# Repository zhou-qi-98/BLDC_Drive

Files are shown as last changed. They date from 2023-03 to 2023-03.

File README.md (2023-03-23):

# 三相无刷直流电机驱动设计

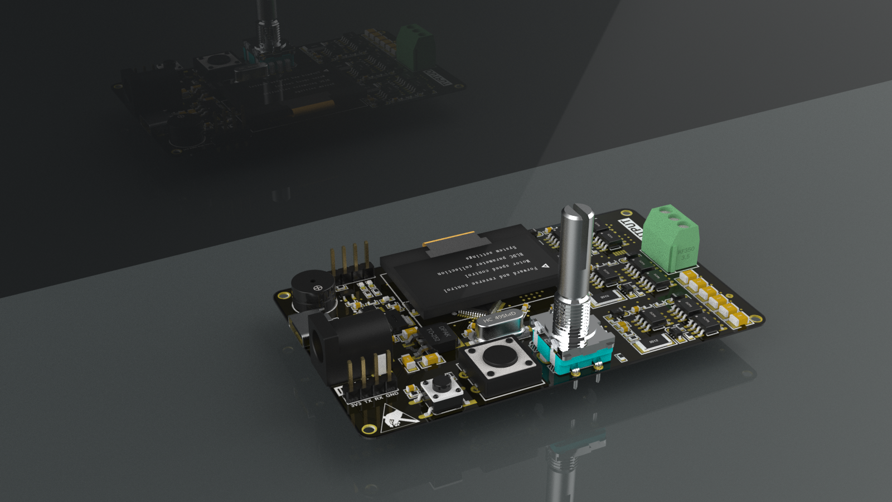
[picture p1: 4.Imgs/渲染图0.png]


#### 介绍
**stm32直流电机控制**
* 采用STM32F103C6T6A作为主控
* 主控与驱动分离
* 采用三相逆变桥电路
* 采集三相电流
* 前级采用栅极驱动MOS，自带闭锁
* 采集电机驱动电压，与MOS电流

无刷直流电机取消了电刷和换向器，从而失去了机械的磁场换向机构，磁场换向通过传感器检测转子位置，利用转子的位置信息来控制由开关电子器件构成的换向电路来达到磁场换向的目的。在无刷直流电机发展伊始，工程师们使用模拟电路来检测转子位置和控制开关器件。随着数字信号处理器、永磁材料和电力电子器件技术的飞速发展，无刷直流电机技术向数字化，智能化迈进。

在现阶段的无刷直流电机的设计中，一款优秀的驱动器设计是十分重要的。驱动器需要正确检测到转子位置信息，而且需要可靠的控制算法来控制功率器件的开通和关断，从而实现精度高、稳定性强的控制效果。

目前，无刷直流电机的主要控制方法有：PID控制、模糊控制、滑模变结构控制、基于神经网络的控制、基于锁相环的控制等。PID控制中P是指比例，I是指积分，D是指微分。通过调整这三个参数，来实现在不同运动状态下生成不同的控制量，来控制对象来达到理想的运动状态。但是由于只有三个可调参数使得控制精度不够，所以导致其在一些需要精密控制的领域不能发挥作用。模糊控制和滑模变结构控制都是非线性的控制方式，模糊控制是运用模糊数学的理论来对一些变量比较多的复杂系统来进行控制，滑模变结构控制是让控制对象在不同的控制逻辑下来回切换，由于此时处于滑动运动状态，对未知干扰的敏感降低，使系统有比较好鲁棒性。其余的控制方式各有特点，在特定领域能对无刷直流电机有良好的控制。

在位置检测领域，一般就有位置传感器检测法和无位置传感器检测法。位置传感器有电磁式的，可以安装在定子组件上，来检测转子永磁体转动，通过磁场的变化记录转子位置信息，也有光电式的，将光源和接收器安装在定子组件上，转子上安装遮光板，当转子转动时，接收器产生的脉冲信号则是转子位置信息。无位置传感器检测法有一种H. Lehuy等人提出的反电动势检测法，这种方法不需要在电机内安装位置传感器，简化了系统的结构。还有一些学者提出过续流二极管法和基于定子磁链估计法等无位置传感器检测法。

#### 六步法
六步法中的三相电机每次只有两组绕组有电流通过，产生磁场。为了让电机旋转，一般按照Q1Q2—Q2Q3—Q3Q4—Q4Q5—Q5Q6—Q6Q1的顺序依次导通功率开关管
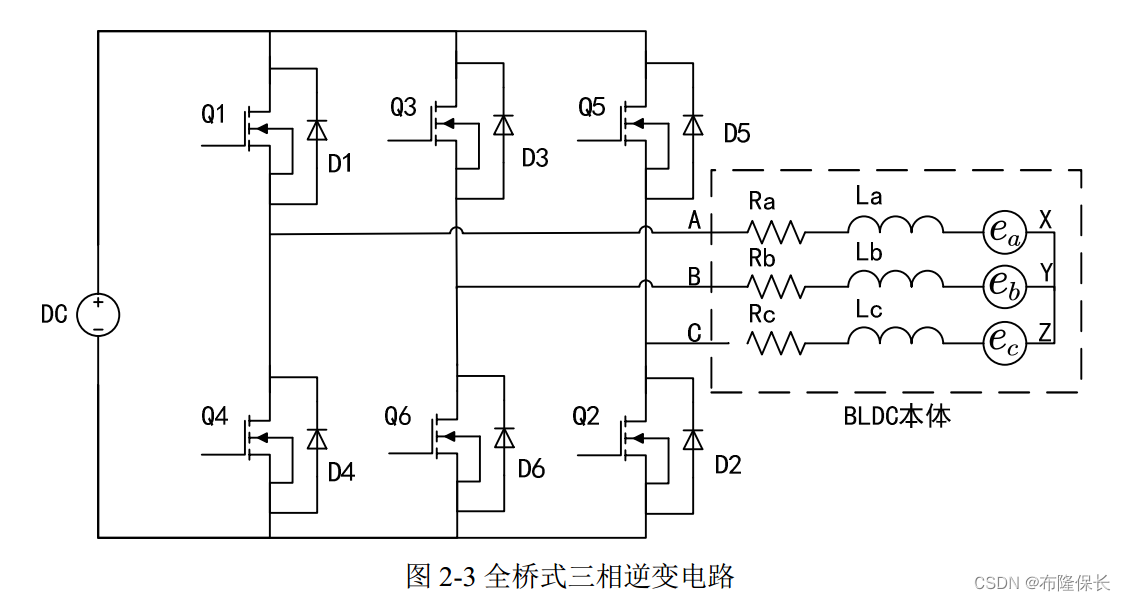
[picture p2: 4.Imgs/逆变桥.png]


#### 反电动势检测法
当转子上的永磁体旋转时，会切割绕组产生反电动势，而且转速越大，其产生的反电动势也越大，这个反电动势是可以使用检测电路检测的。检测三相绕组中反电动势，根据其变化，就可以得知转子是否到达六个关键换向节点，并决定是否进行换相操作。

无刷直流电机产生的反电动势是呈梯形波形状的，而其定子电流是断续的方波形状。因为在电机转动过程中，定子中总有两相绕组会通过电流，使那两相绕组中也会生成大小相等、方向相反的反电动势。等其中一相绕组断开时，其电流立即降为零，但是反电动势会通过开关管和二极管进行续流，会由正变负或者由负变正，与下一段电流反向时的反电动势接续。在一个周期中，每相的反电动势有两次过零点，三相则可以接收到6次过零点信号，滞后30°+60°k（k=0，1，2…）后即为开关管换相的信号。
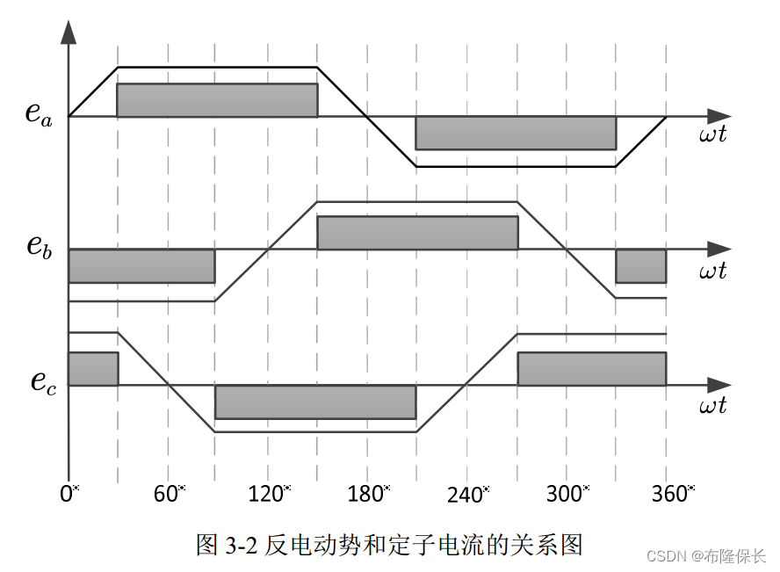
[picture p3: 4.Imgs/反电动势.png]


#### 原理图
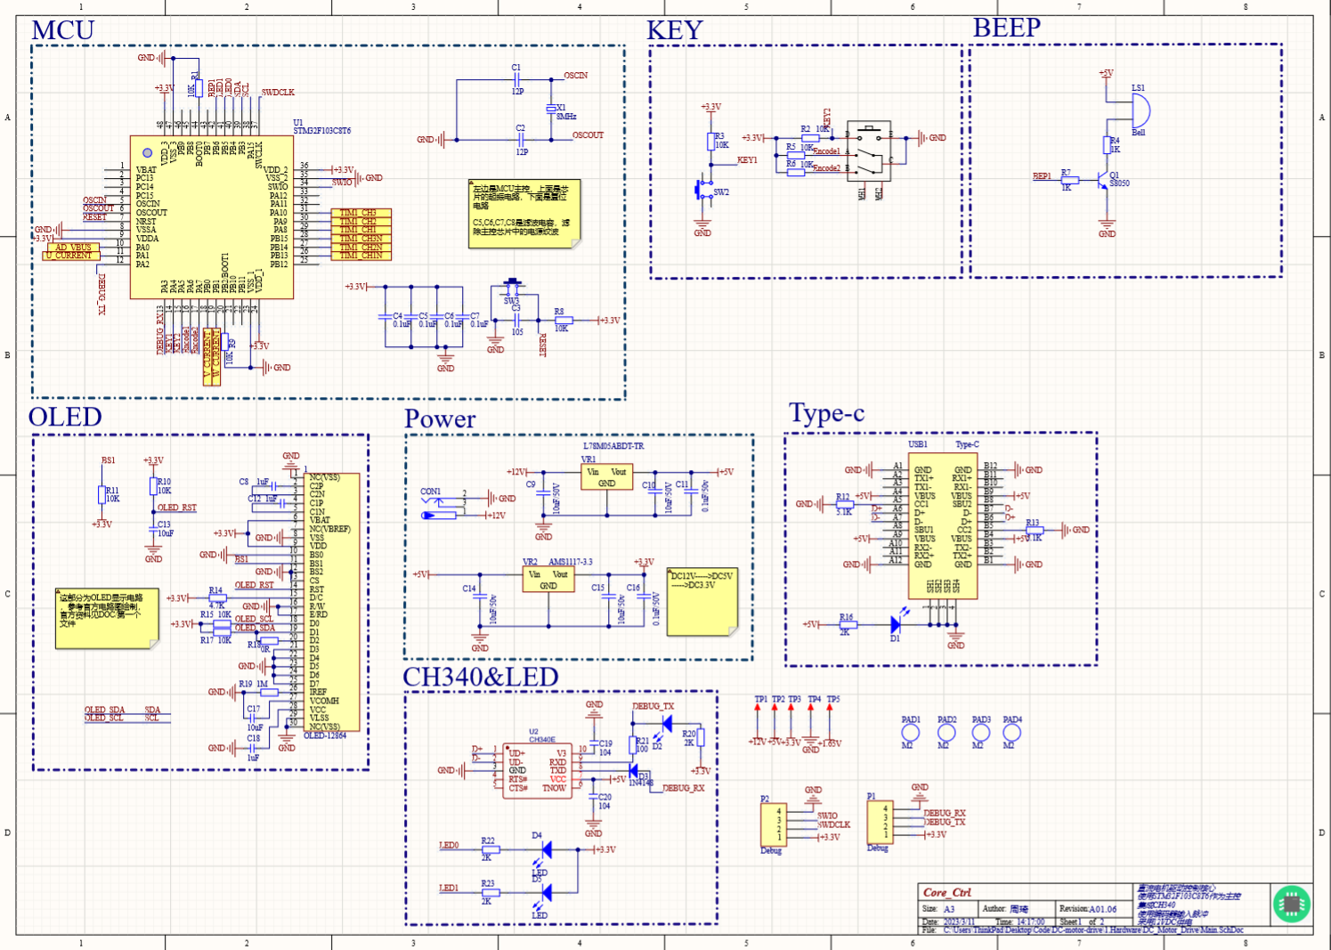
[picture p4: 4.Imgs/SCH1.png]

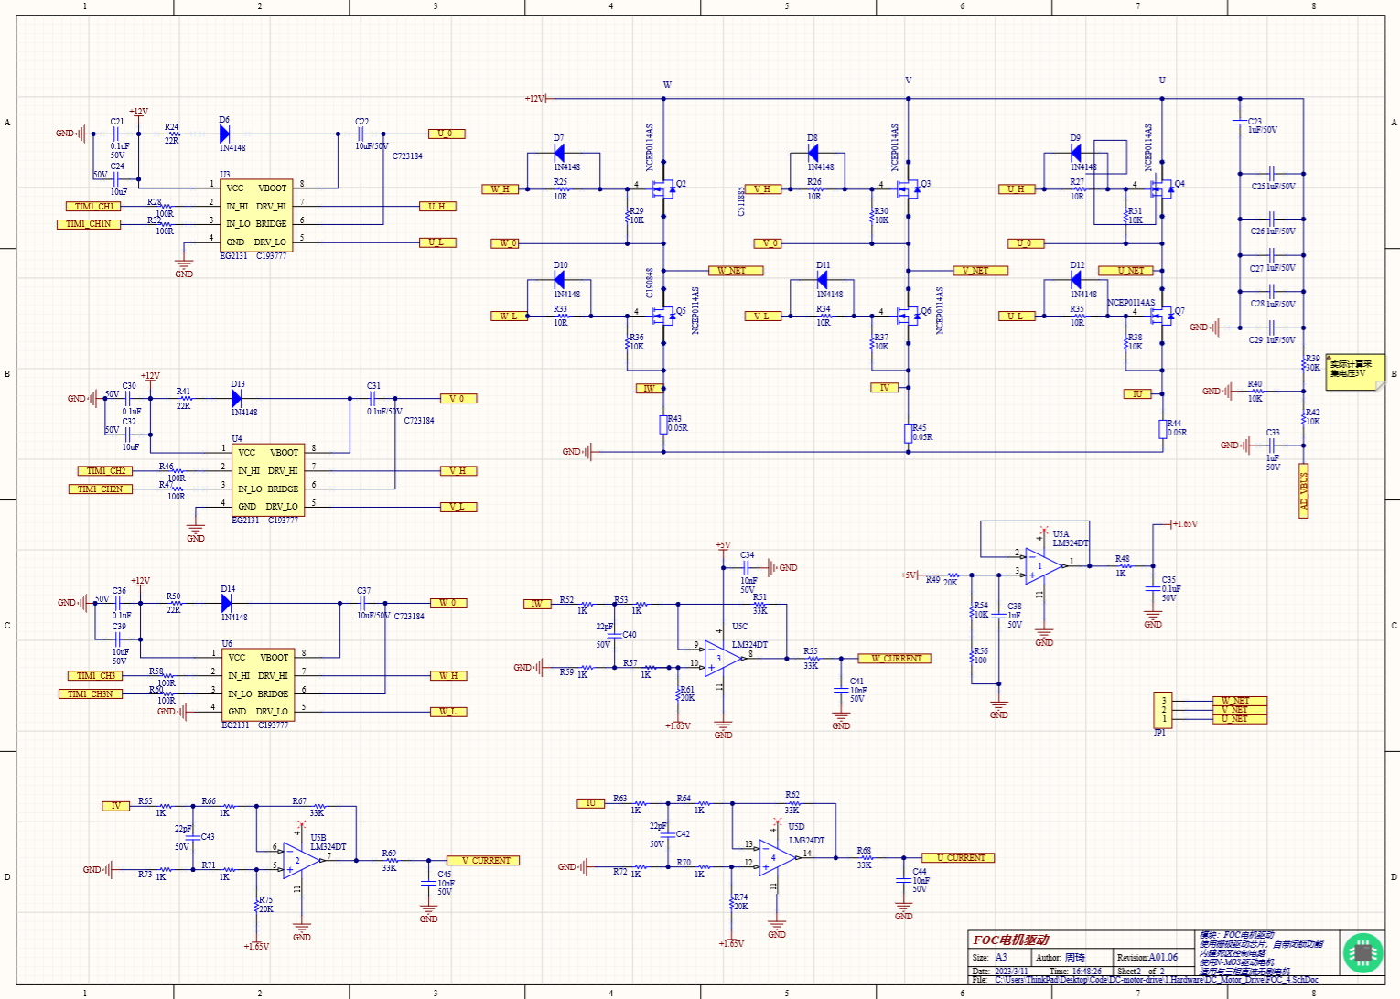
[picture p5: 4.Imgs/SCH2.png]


#### PCB
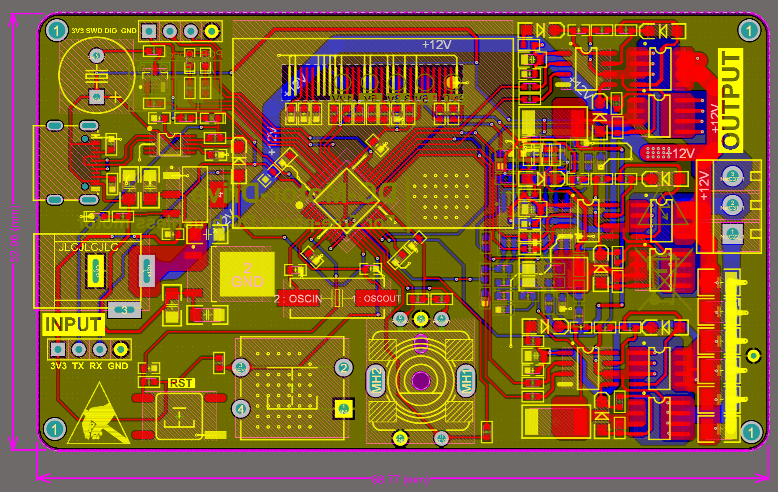
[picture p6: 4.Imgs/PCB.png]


#### 软件架构
* 分时调度

#### 参与贡献
* [爱学习的王大可](https://gitee.com/zhouqi98)
* [幺幺零1223](https://gitee.com/one-zero-1223)

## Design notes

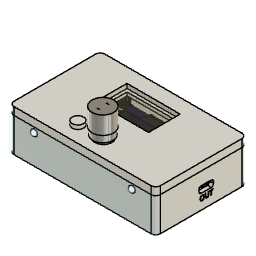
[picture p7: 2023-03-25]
1.Hardware/DC_Motor1 v24.png

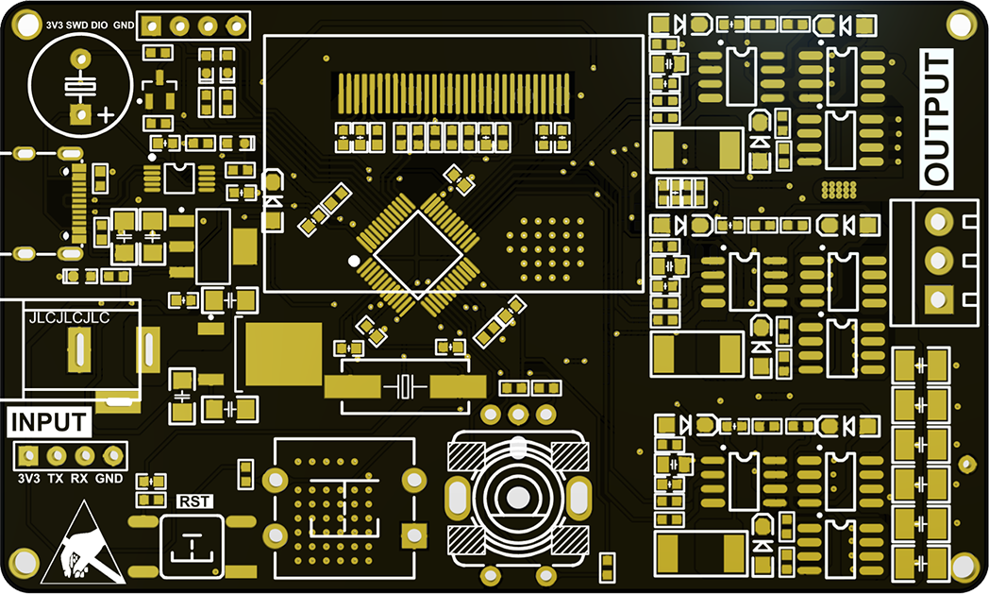
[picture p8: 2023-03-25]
4.Imgs/贴图3.png

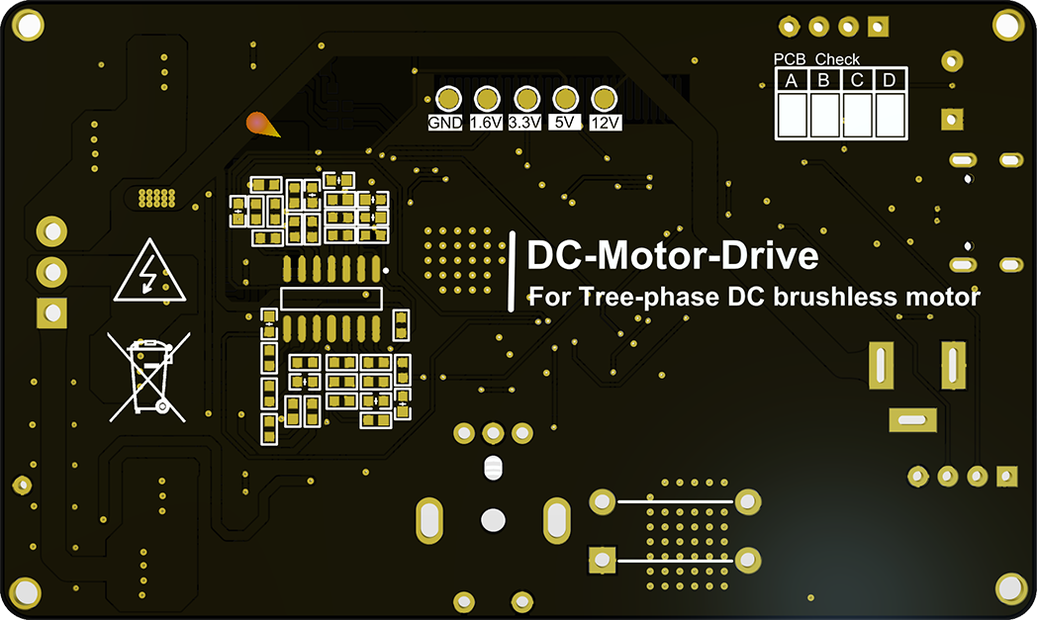
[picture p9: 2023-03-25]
4.Imgs/贴图4.png

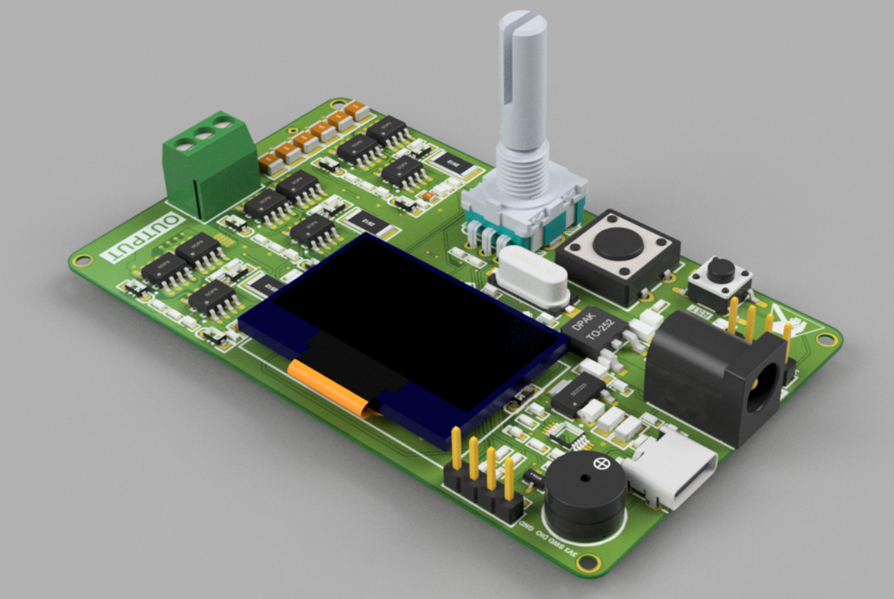
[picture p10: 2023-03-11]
4.Imgs/渲染图1.png

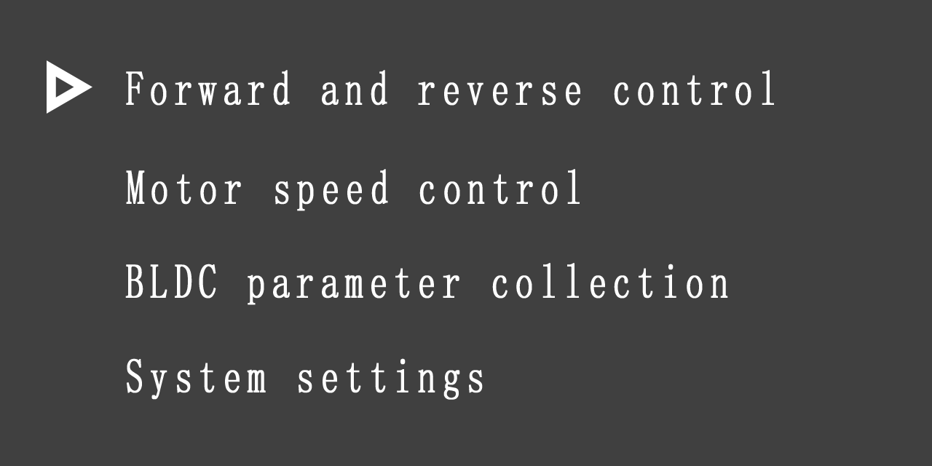
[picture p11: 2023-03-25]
4.Imgs/oled.png

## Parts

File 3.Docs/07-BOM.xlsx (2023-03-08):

Comment | Description | Designator | Footprint | LibRef | Quantity
OLED-12864 | 显示屏 | 1 | OLED-12864-1.3-TOP | OLED-12864 | 1
12P | 贴片电容 | C1, C2 | C0603_L | C | 2
105 | 贴片电容 | C3 | C0603_L | C | 1
0.1uF | 贴片电容, [NoValue] | C4, C5, C6, C7, C21, C30, C35, C36 | C0603_L | C, Cap | 8
1uF | Capacitor, [NoValue] | C8, C12, C18, C33, C38 | C0603_L | 电容-0402, Cap | 5
10uF/50V | C89632, [NoValue] | C9, C10, C14, C15 | C1206_L | Cap | 4
0.1uF/50v |  | C11 | C1206_L | Cap | 1
10uF | Capacitor | C13, C17 | C0603_L | 电容-0402 | 2
0.1uF/50V | C89632 | C16, C31 | C0603_L | Cap | 2
104 | 无极性贴片电容 | C19, C20 | C0603_L | C | 2
10uF/50V | C89632 | C22, C37 | C0603_L | Cap | 2
1uF/50V |  | C23, C25, C26, C27, C28, C29 | C1210_L | Cap | 6
10uF |  | C24, C32, C39 | C0805_L | Cap | 3
10nF |  | C34, C41, C44, C45 | C0603_L | Cap | 4
22pF |  | C40, C42, C43 | C0603_L | Cap | 3
3.5*1.3 | 低压电源接口 | CON1 | DC-005 | P-DC | 1
LED0 | 发光二极管 | D1 | LED0603_R | LED0 | 1
LED0 | 发光二极管 | D2 | LED0603_G | LED0 | 1
1N4148 | 整流二极管, 二极管 | D3, D6, D7, D8, D9, D10, D11, D12, D13, D14 | SOD-123 | M7, SOD-323 1N4148WS T4 | 10
LED | 发光二极管 | D4, D5 | LED0603_B | LED | 2
HDR-1X3 | 3P接插件 | JP1 | KF350-3P | Header 3 | 1
Bell | Electrical Bell | LS1 | BEEP 5x9x5.5 | Bell | 1
Debug | Header, 4-Pin | P1, P2 | HDR2.54-LI-4P | Header 4 | 2
M2 | 铜柱孔 | PAD1, PAD2, PAD3, PAD4 | M2 | M3 | 4
S8050 | 高频放大-NPN型 | Q1 | SOT23-3N | 8050-SMD | 1
NCEP0114AS | C190848 | Q2, Q3, Q4, Q5, Q6, Q7 | SOP8 | NMOS-2 | 6
10K | 贴片电阻, Resistor | R1, R2, R3, R5, R6, R8, R9, R10, R11, R15, R17, R29, R30, R31, R36, R37, R38, R40, R42, R54 | R0603_L | R, 电阻-0402, Res1 | 20
1K | Resistor | R4, R7, R48, R52, R53, R57, R59, R63, R64, R65, R66, R70, R71, R72, R73 | R0603_L | 电阻-0402, Res1 | 15
5.1K | Resistor | R12, R13 | R0603_L | 电阻-0402 | 2
4.7K | Resistor | R14 | R0603_L | 电阻-0402 | 1
2K | Resistor, 贴片电阻 | R16, R20, R22, R23 | R0603_L | 电阻-0402, R | 4
0R | Resistor | R18 | R0603_L | 电阻-0402 | 1
1M | Resistor | R19 | R0603_L | 电阻-0402 | 1
100 | Resistor | R21, R56 | R0603_L | 电阻-0402, Res1 | 2
22R | Resistor | R24, R41, R50 | R0603_L | Res1 | 3
10R | Resistor | R25, R26, R27, R33, R34, R35 | R0603_L | Res1 | 6
100R | Resistor | R28, R32, R46, R47, R58, R60 | R0603_L | Res1 | 6
30K | Resistor | R39 | R0603_L | Res1 | 1
0.05R | 电流检测电阻 | R43, R44, R45 | R2512_L | R-I | 3
20K | Resistor | R49, R61, R74, R75 | R0603_L | Res1 | 4
33K | Resistor | R51, R55, R62, R67, R68, R69 | R0603_L | Res1 | 6
EC11K1524406 |  | SW1 | SW-TH_EC11K1524406 | EC11K1524406 | 1
12x12x5 | 直插12x12轻触开关 | SW2 | SW DIP-12*12*4.3 | TSW DIP-12x12 | 1
6x6x5 | 贴片6x6轻触开关 | SW3 | SW SMD-6*6*5 | TSW SMD-6x6 | 1
TEST | 测试点 | TP1, TP2, TP3, TP4, TP5 | TEST 1.6 | TEST | 5
STM32F103C8T6 |  | U1 | LQFP48-7*7 | STM32F103C8T6 | 1
CH340E |  | U2 | MSOP10_M | CH340E | 1
EG2131 | C193777 | U3, U4, U6 | SOP8 | NCP5106BDR2G | 3
LM324DT | 运放 | U5 | SOIC-14 | LM324DT_[C71035] | 1
Type-C |  | USB1 | USB-C-SMD_16P | USB-Type-C-TOP | 1
L78M05ABDT-TR | 低压差线性稳压(LDO) | VR1 | TO-252 | TO-252-2 L78M05ABDT-TR | 1
AMS1117-3.3 | 低压差线性稳压(LDO) | VR2 | SOT223_L | SOT-223 AMS1117-3.3 | 1
8MHz | 2脚无源脚晶振 | X1 | OSC HC-49SMD | XTAL-2P | 1

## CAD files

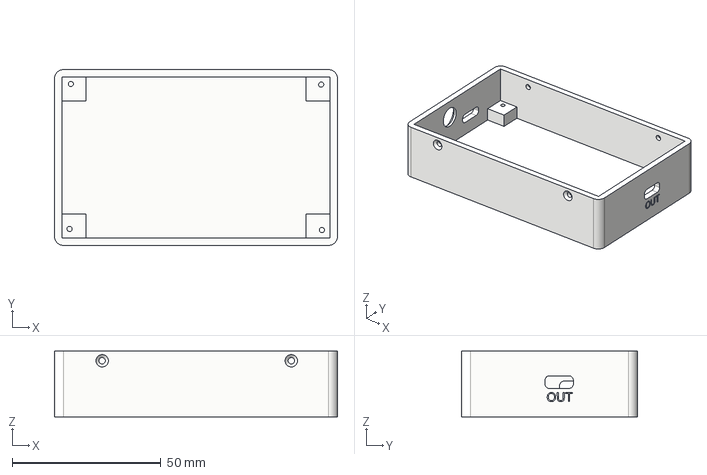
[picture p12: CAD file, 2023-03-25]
1.Hardware/底部.step
95.0 x 59.0 x 22.0 mm

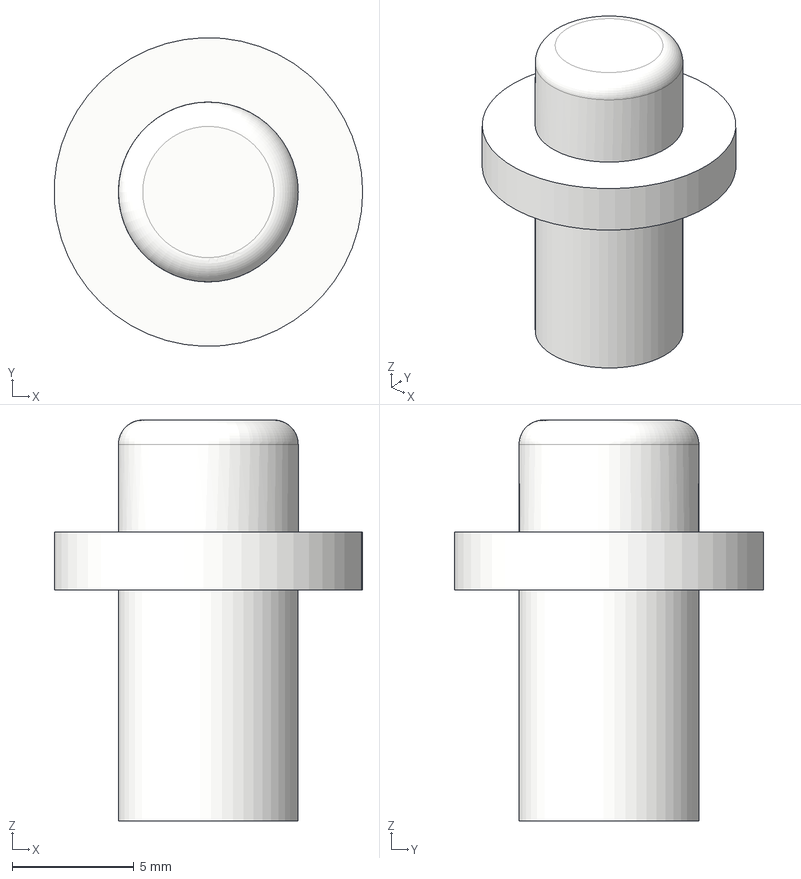
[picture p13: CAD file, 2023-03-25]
1.Hardware/按钮.step
12.7 x 12.7 x 16.5 mm

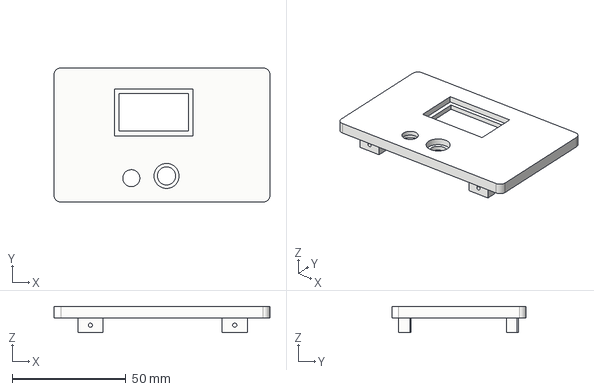
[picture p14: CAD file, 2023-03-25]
1.Hardware/盖子.step
95.0 x 59.0 x 11.5 mm

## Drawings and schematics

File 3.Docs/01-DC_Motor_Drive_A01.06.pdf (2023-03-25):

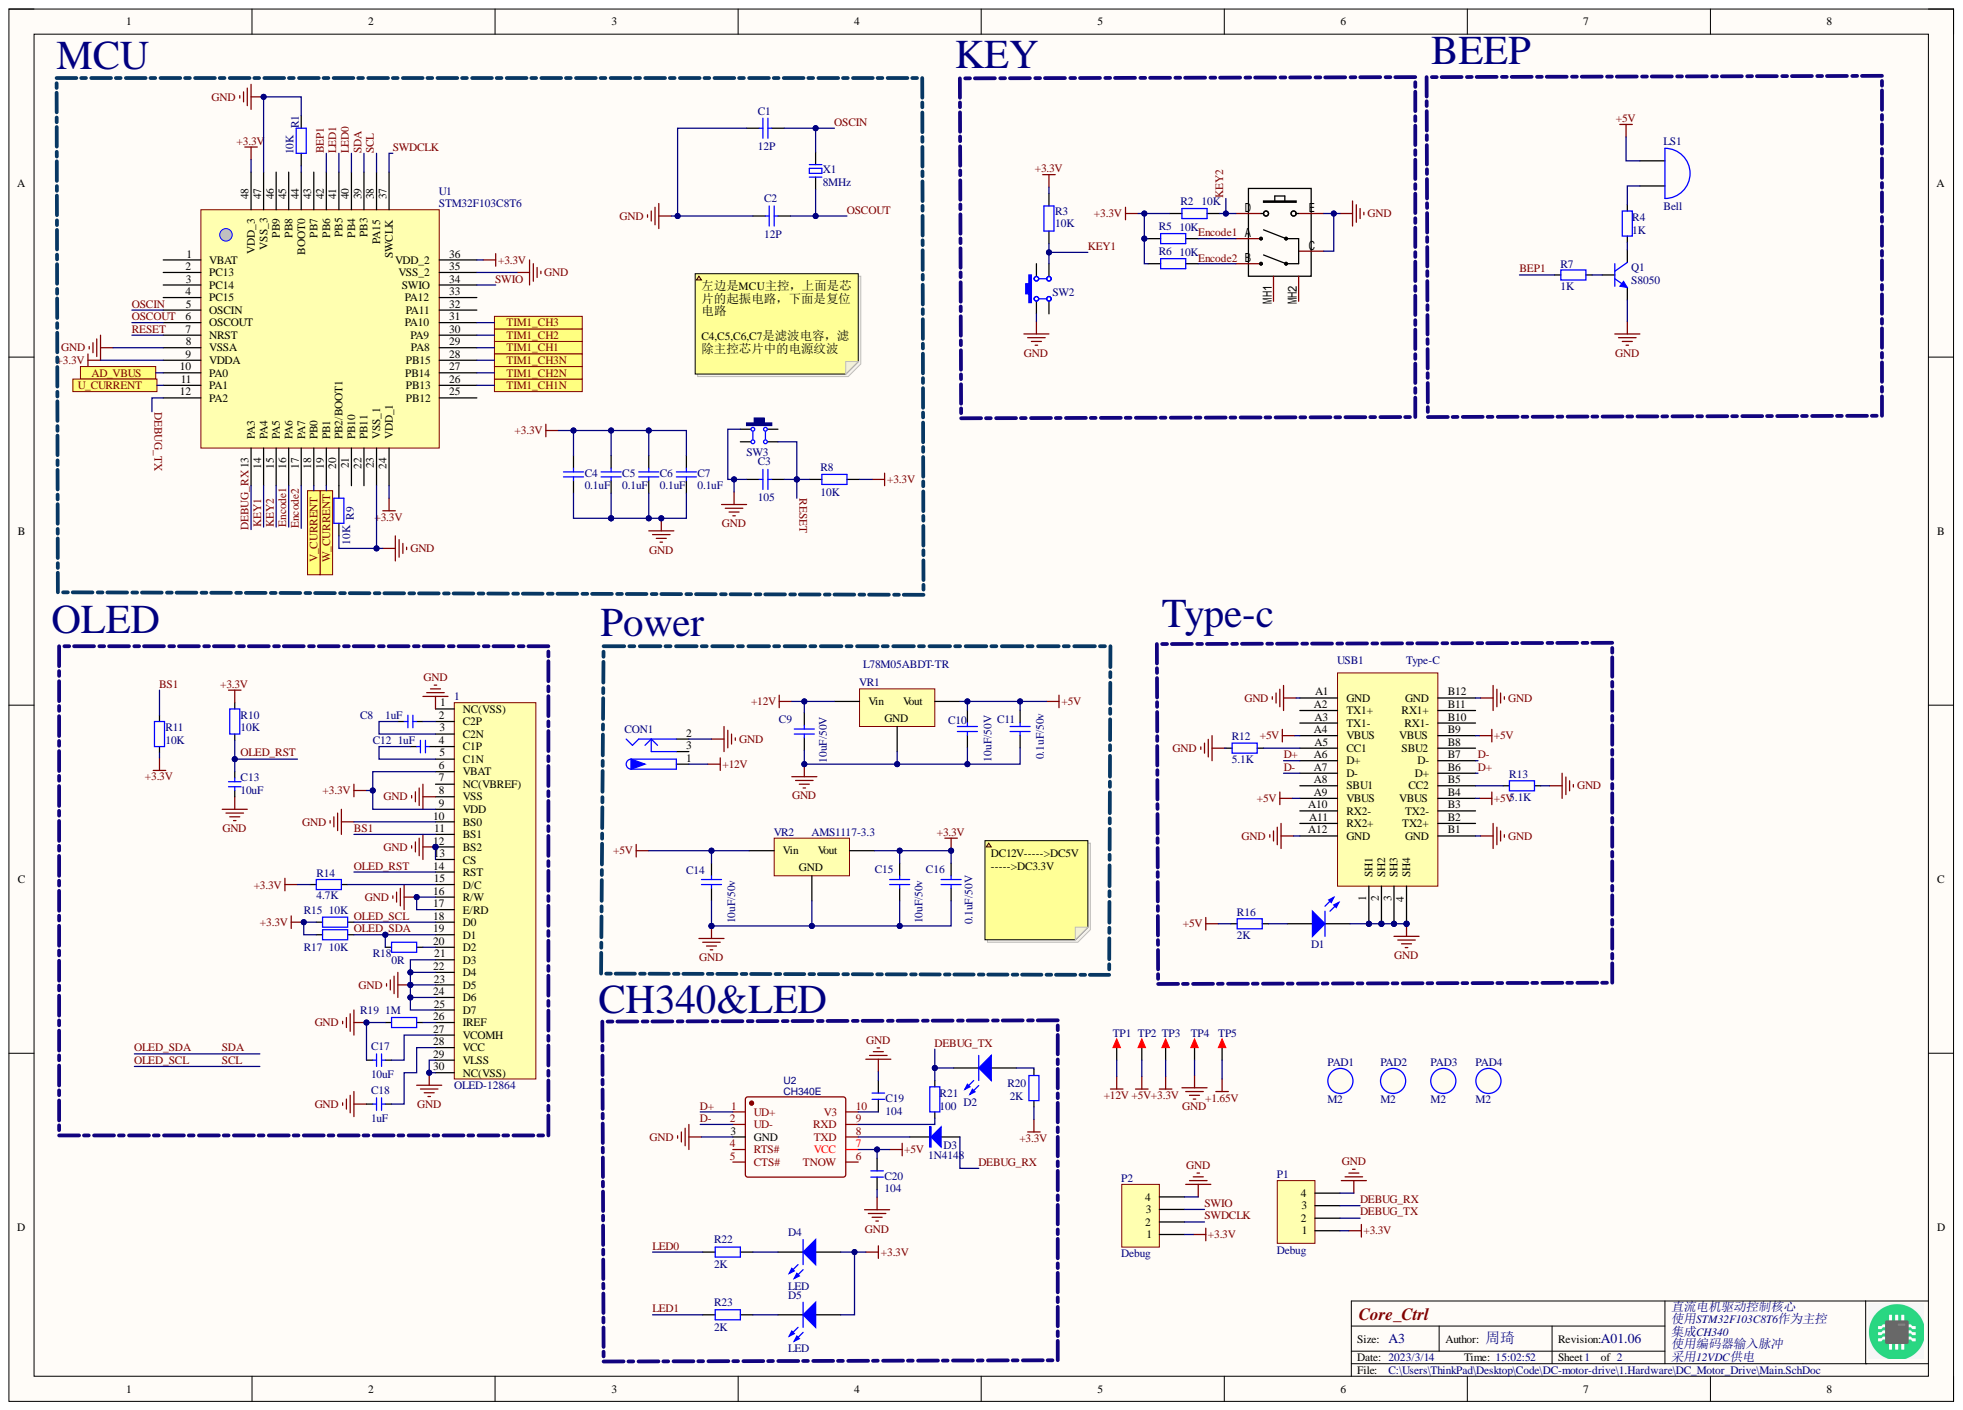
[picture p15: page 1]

左边是MCU主控，上面是芯 片的起振电路，下面是复位

VDDA 9 | | TIM1_CH3N

AD_VBUS | | PA1 11 | | TIM1_CH2N
U_CURRENT | | | | TIM1_CH1N

C17 | | VCOMH 27

VCC 28
VLSS 29
NC(VSS) 30

C:\Users\ThinkPad\Desktop\Code\DC-motor-drive\1.Hardware\DC_Motor_Drive\Main.SchDoc

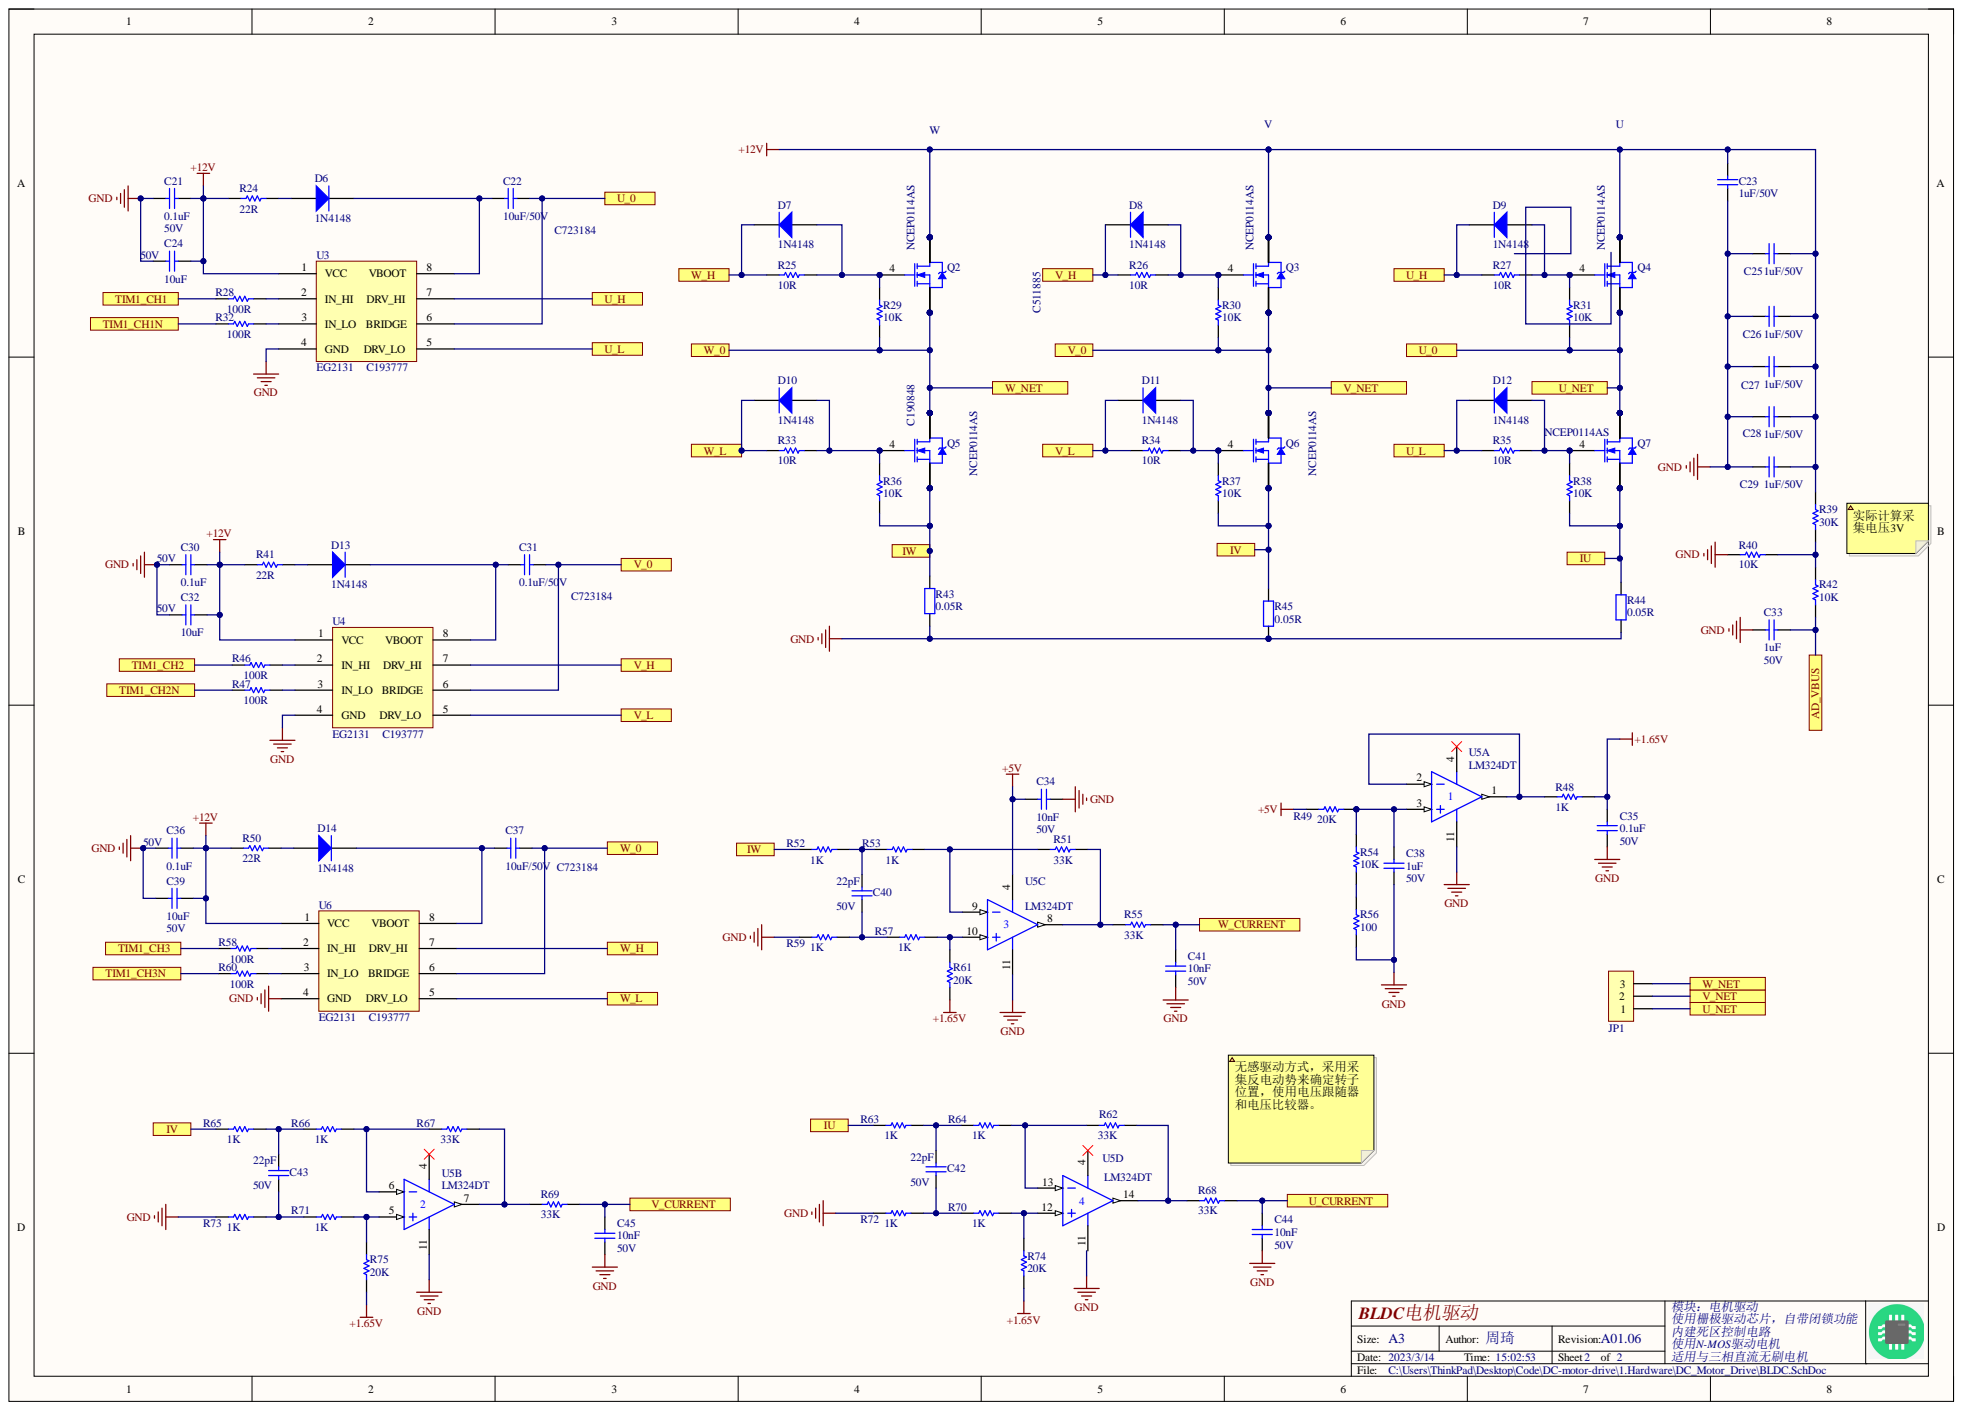
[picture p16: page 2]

C:\Users\ThinkPad\Desktop\Code\DC-motor-drive\1.Hardware\DC_Motor_Drive\BLDC.SchDoc

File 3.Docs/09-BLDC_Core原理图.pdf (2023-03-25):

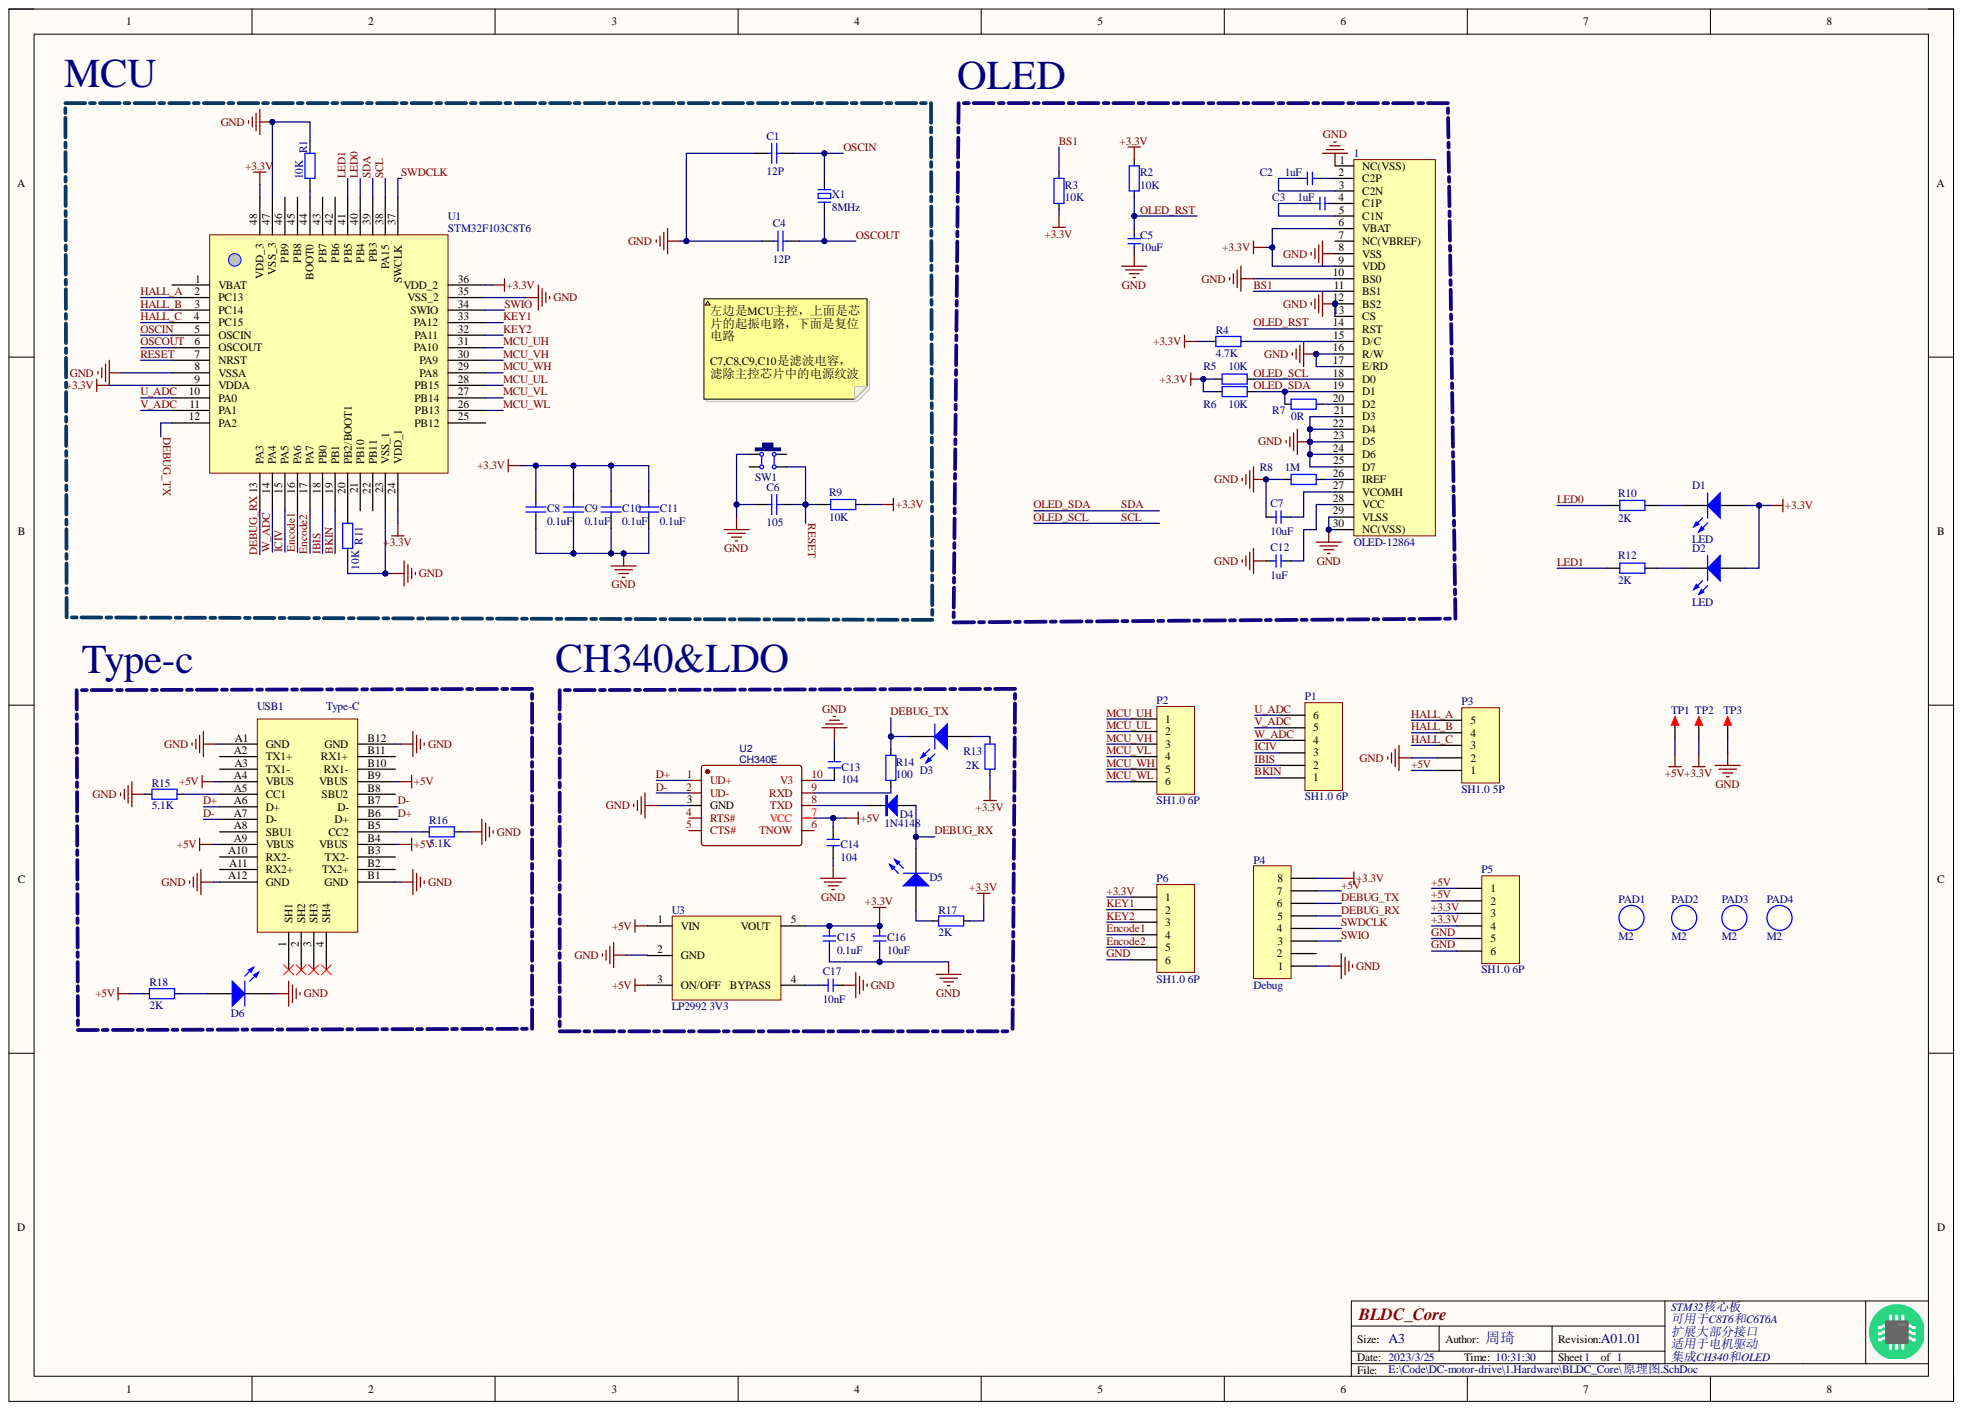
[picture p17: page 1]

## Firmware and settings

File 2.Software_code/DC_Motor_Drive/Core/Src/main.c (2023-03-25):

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
/* Includes ------------------------------------------------------------------*/
#include "main.h"
#include "adc.h"
#include "iwdg.h"
#include "tim.h"
#include "usart.h"
#include "gpio.h"

/* USER CODE BEGIN Includes */
//以下开始用户头文件，这里的头文件在MY文件夹内
#include "stdio.h"
#include "User_Scheduler.h"
#include "User_Function.h"
#include "IIC_OLED.h"
#include "key.h"
#include "bmp.h"
#include "Motor.h"
/* USER CODE END Includes */

/* USER CODE BEGIN PD */
#define VERSION      "A01.0D"//主版本号子版本号.修正版本号

/*---->
版本更新历史
A01.0D: 新增速度变量，实现编码器控制 2023/3/25 13:18
A01.0C: 多级菜单功能完成 2023/3/24 20:36
A01.0B: 编码器功能初步测试通过 2023/3/15 21:39
A01.0A: 调度器/OLED等外设测试通过 2023/3/15 20:49
A01.09: 新增按键扫描函数(待验证) 2023/3/14 14:08
A01.08: 新增ADC校准，规范代码(待验证) 2023/3/11 17:19
A01.07: 新增看门狗，溢出时间约6.5s(待验证) 2023/3/11 16:42
A01.06: 采集四个通道的ADC数据(待验证) 2023/3/11 16:30
A01.05: OLED移植成功(待验证) 2023/3/11 15:54
A01.04: 新增用户调度器(未验证) 2023/3/11 15:36
A01.03: 重写printf函数，修改至串口二 2023/3/11 15:19
A01.02: 宏定义管LED,BEEP外设管脚 2023/3/11 15:06
A01.01: 新建工程，初始化外设 2023/3/11 14:55
*/

/* USER CODE END PD */

/* USER CODE BEGIN PM */
volatile uint8_t SYS_TIME1S_FLAG = 0;//计数1s标志位
int8_t led_status;
/* USER CODE END PM */


void SystemClock_Config(void);
/* USER CODE BEGIN 0 */
/*-----------------------------------------*/
/*-----重定义printf函数--------------------*/
/*-----函数名：int fputc(int ch, FILE *f)--*/
/*-----------------------------------------*/
int fputc(int ch, FILE *f){
	uint8_t temp[1] = {ch};
	HAL_UART_Transmit(&huart2, temp, 1, 2);//huart2需要根据你的配置修改
	return ch;
}

/* USER CODE END 0 */

/**
  * @brief  The application entry point.
  * @retval int
  */
int main(void)
{
  /* MCU Configuration--------------------------------------------------------*/

  /* Reset of all peripherals, Initializes the Flash interface and the Systick. */
  HAL_Init();

  /* Configure the system clock */
  SystemClock_Config();

  /* Initialize all configured peripherals */
  MX_GPIO_Init();
  MX_TIM3_Init();
  MX_ADC1_Init();
  MX_TIM1_Init();
  MX_USART2_UART_Init();
  MX_IWDG_Init();
  MX_TIM2_Init();
  /* USER CODE BEGIN 2 */
	HAL_TIM_Base_Start_IT(&htim2);//开启定时器
  __HAL_TIM_CLEAR_IT(&htim3,TIM_IT_UPDATE);

	HAL_TIM_Encoder_Start(&htim3, TIM_CHANNEL_ALL);//启动计数
  __HAL_TIM_ENABLE_IT(&htim3,TIM_IT_UPDATE);

	HAL_ADCEx_Calibration_Start(&hadc1); //ADC校准

	BEEP_OFF;
	OLED_Init();			//OLED初始化
	OLED_CLS();				//OLED清屏
	//OLED_ShowStr(16,4,(unsigned char*)"SYS init succeeded      ",1);
	OLED_DrawBMP(0,0,128,8,BMP0);
	user_main_info("System initialization succeeded！");
	//MX_IWDG_Init();
	
	//HAL_TIM_PWM_Start(&htim1,TIM_CHANNEL_1);
  //HAL_TIMEx_PWMN_Start(&htim1,TIM_CHANNEL_1);
  //HAL_TIM_PWM_Start(&htim1,TIM_CHANNEL_2);
  //HAL_TIMEx_PWMN_Start(&htim1,TIM_CHANNEL_2);

	
	

	//TIM1->CCR1 = 50;//50%的占空比
	//HAL_TIM_PWM_Start(&htim1,TIM_CHANNEL_1);//V相正波
	/*
				HAL_TIM_PWM_Stop(&htim1,TIM_CHANNEL_1);//U相不发波
			HAL_TIMEx_PWMN_Stop(&htim1,TIM_CHANNEL_1);
			
			TIM1->CCR2 = 50;//50%的占空比
			HAL_TIM_PWM_Start(&htim1,TIM_CHANNEL_2);//V相正波
			
			TIM1->CCR3 = 50;//50%的占空比
			HAL_TIMEx_PWMN_Start(&htim1,TIM_CHANNEL_3);//V相正波
			*/
	
	//MX_IWDG_Init();
	//LED0_ON;
	
	
	/*开始控制电机*/
	//Motor_Stop();
	//ROTOR_Pre_positioning(1);
	//Motor_Start(1);
	
	
	
  /* USER CODE END 2 */

  /* Infinite loop */
  /* USER CODE BEGIN WHILE */
  while (1)
  {
    /* USER CODE END WHILE */

    /* USER CODE BEGIN 3 */
		Schedule();						/*调度器*/
		FuncRun(&tSysScanFlag);/*功能运行*/
		//Motor_Run(1);
		
  }
  /* USER CODE END 3 */
}

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
/* USER CODE BEGIN 4 */
/*下面开始子函数*/
/*中断服务函数*/
void HAL_TIM_PeriodElapsedCallback(TIM_HandleTypeDef *htim) 
	{
			if (htim->Instance == htim2.Instance) {//定时器2中断,这里1ms中断一次
					SYS_TIME1S_FLAG=1;
	    }
      if (htim->Instance == htim3.Instance)//外部中断3来源于编码器
      {
        
        if( ((int)(__HAL_TIM_IS_TIM_COUNTING_DOWN(&htim3)))== 0)//反向旋转
        {
          KEY_Value = 4;
        }else//正向旋转
        {
          KEY_Value = 3;
        }
        //user_main_info("编码器%d",KEY_Value);
      }

}
	



/* USER CODE END 4 */
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


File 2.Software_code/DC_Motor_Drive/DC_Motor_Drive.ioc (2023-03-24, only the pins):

Mcu.UserName=STM32F103C6Tx
PA0-WKUP.Signal=ADCx_IN0
PA1.Signal=ADCx_IN1
PA10.GPIO_Label=WH
PA10.Signal=GPIO_Output
PA13.Signal=SYS_JTMS-SWDIO
PA14.Signal=SYS_JTCK-SWCLK
PA15.GPIO_Label=IIC_SCL
PA15.Signal=GPIO_Output
PA2.Signal=USART2_TX
PA3.Signal=USART2_RX
PA4.GPIO_Label=KEY1
PA4.Signal=GPIO_Input
PA5.GPIO_Label=KEY2
PA5.Signal=GPIO_Input
PA6.Signal=S_TIM3_CH1
PA7.Signal=S_TIM3_CH2
PA8.GPIO_Label=UH
PA8.Signal=GPIO_Output
PA9.GPIO_Label=VH
PA9.Signal=GPIO_Output
PB0.Signal=ADCx_IN8
PB1.Signal=ADCx_IN9
PB13.GPIO_Label=UL
PB13.Signal=GPIO_Output
PB14.GPIO_Label=VL
PB14.Signal=GPIO_Output
PB15.GPIO_Label=WL
PB15.Signal=GPIO_Output
PB3.GPIO_Label=IIC_SDA
PB3.Signal=GPIO_Output
PB4.GPIO_Label=LED0
PB4.Signal=GPIO_Output
PB5.GPIO_Label=LED1
PB5.Signal=GPIO_Output
PB6.GPIO_Label=BEEP1
PB6.Signal=GPIO_Output
PD0-OSC_IN.Signal=RCC_OSC_IN
PD1-OSC_OUT.Signal=RCC_OSC_OUT

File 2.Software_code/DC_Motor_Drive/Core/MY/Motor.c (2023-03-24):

#include "Motor.h"

/*
//order 用于发波的标号
void Motor_run(uint8_t order,uint8_t Duty)
{
	switch(order)
	{
		//U0  V+ W-
		case 1:
		{
			HAL_TIM_PWM_Stop(&htim1,TIM_CHANNEL_1);//U相不发波
			HAL_TIMEx_PWMN_Stop(&htim1,TIM_CHANNEL_1);
			
			TIM1->CCR2 = ((float)Duty/(float)100)*70;//修改占空比
			HAL_TIM_PWM_Start(&htim1,TIM_CHANNEL_2);//V相正波
			
			TIM1->CCR3 = ((float)Duty/(float)100)*70;//50%的占空比
			HAL_TIMEx_PWMN_Start(&htim1,TIM_CHANNEL_3);//W相互补波
			break;	
		}
		
		case 3:
		{
			HAL_TIM_PWM_Stop(&htim1,TIM_CHANNEL_2);//v相不发波
			HAL_TIMEx_PWMN_Stop(&htim1,TIM_CHANNEL_2);
			
			TIM1->CCR1 = ((float)Duty/(float)100)*70;//修改占空比
			HAL_TIMEx_PWMN_Start(&htim1,TIM_CHANNEL_1);//V相互补波
			
			TIM1->CCR3 = ((float)Duty/(float)100)*70;//50%的占空比
			HAL_TIM_PWM_Start(&htim1,TIM_CHANNEL_3);//W相正波
			break;	
		}
		
		case 2:
		{
			HAL_TIM_PWM_Stop(&htim1,TIM_CHANNEL_3);//W相不发波
			HAL_TIMEx_PWMN_Stop(&htim1,TIM_CHANNEL_3);
			
			TIM1->CCR1 = ((float)Duty/(float)100)*70;//修改占空比
			HAL_TIMEx_PWMN_Start(&htim1,TIM_CHANNEL_1);//U相互补波
			
			TIM1->CCR2 = ((float)Duty/(float)100)*70;//50%的占空比
			HAL_TIM_PWM_Start(&htim1,TIM_CHANNEL_2);//V相正波
			break;	
		}
		case 6:
		{
			HAL_TIM_PWM_Stop(&htim1,TIM_CHANNEL_1);//U相不发波
			HAL_TIMEx_PWMN_Stop(&htim1,TIM_CHANNEL_1);
			
			TIM1->CCR3 = ((float)Duty/(float)100)*70;//修改占空比
			HAL_TIMEx_PWMN_Start(&htim1,TIM_CHANNEL_3);//U相互补波
			
			TIM1->CCR2 = ((float)Duty/(float)100)*70;//修改占空比
			HAL_TIM_PWM_Start(&htim1,TIM_CHANNEL_2);//V相正波
			break;	
		}
		case 4:
		{
			HAL_TIM_PWM_Stop(&htim1,TIM_CHANNEL_2);//V相不发波
			HAL_TIMEx_PWMN_Stop(&htim1,TIM_CHANNEL_2);
			
			TIM1->CCR3 = ((float)Duty/(float)100)*70;//修改占空比
			HAL_TIMEx_PWMN_Start(&htim1,TIM_CHANNEL_3);//W相互补波
			
			TIM1->CCR1 = ((float)Duty/(float)100)*70;//修改占空比
			HAL_TIM_PWM_Start(&htim1,TIM_CHANNEL_1);//U相正波
			break;	
		}
		case 5:
		{
			HAL_TIM_PWM_Stop(&htim1,TIM_CHANNEL_3);//W相不发波
			HAL_TIMEx_PWMN_Stop(&htim1,TIM_CHANNEL_3);
			
			TIM1->CCR2 = ((float)Duty/(float)100)*70;//修改占空比
			HAL_TIMEx_PWMN_Start(&htim1,TIM_CHANNEL_2);//V相互补波
			
			TIM1->CCR1 = ((float)Duty/(float)100)*70;//修改占空比
			HAL_TIM_PWM_Start(&htim1,TIM_CHANNEL_1);//V相正波
			break;	
		}
		default:break;
	}
}

*/
// 120 度HAL,如果你的电机直接用这个表驱动有问，那你可能需要根据
// 实际电机进行适当的调整对应关系，可在该表基础上进行适当修改即可
// 正 转
// 霍尔#1 霍尔#2 霍尔#3		A+ 		A- 		 B+ 		B- 		C+ 		C- 		方向
// 1 				0 		1 		关闭 		关闭 	关闭 	开通 	开通 		关闭 		↓   
// 0 				0 		1 		关闭 		开通 	关闭 	关闭 	开通 		关闭 		↓		
// 0 				1 		1 		关闭 		开通 	开通 	关闭 	关闭 		关闭 		↓			
// 0 				1 		0 		关闭 		关闭 	开通 	关闭 	关闭 		开通 		↓
// 1 				1 		0 		开通 		关闭 	关闭 	关闭 	关闭 		开通 		↓
// 1 				0 		0 		开通 		关闭 	关闭 	开通 	关闭 		关闭 		↓

// 反 转
// 霍尔#1 霍尔#2 霍尔#3 	A+ 		A- 			B+ 		B- 		C+ 		C- 		方向
// 1 				0 		1 		关闭 		关闭 	开通 	关闭 	关闭 		开通 		↑
// 0 				0 		1 		开通 		关闭 	关闭 	关闭 	关闭 		开通 		↑
// 0 				1 		1 		开通 		关闭 	关闭 	开通 	关闭 		关闭 		↑
// 0 				1 		0 		关闭 		关闭 	关闭 	开通 	开通 		关闭 		↑
// 1 				1 		0 		关闭 		开通 	关闭 	关闭 	开通 		关闭 		↑
// 1 				0 		0 		关闭 		开通 	开通 	关闭 	关闭 		关闭 		↑



/*
电机停机
*/
void Motor_Stop()
{
	//关三个上管，开三个下管，泄除反电动势
	
	//1.关上管
	UH_OFF;VH_OFF;WH_OFF;
	HAL_Delay(1);//延时下，防止上管未完全关闭 就导通下管，烧毁MOS
	//2.开下管
	UL_ON;VL_ON;WL_ON;	
}



/*
电机转子预定位
direction:转动方向，根据转动方向来进行调整
做三次预定位，确定转子定位到准确位置
*/
void ROTOR_Pre_positioning(uint8_t direction)
{
	if(direction)//正转
	{
			//1.开始做预定位
		for(uint8_t i = 0;i<3;i++)
		{
			UH_ON;VH_OFF;WH_OFF;//U+ W-
			UL_OFF;VL_OFF;WL_ON;
			HAL_Delay(10);
		}
			//此时转自应该在位置6	
	}
}


void Six_step(uint8_t step)
{
	switch(step)
	{
		case 1:
		{
			UH_ON;VH_OFF;WH_OFF;//U+ V-
			UL_OFF;VL_ON;WL_OFF;
			break;
		}
		case 2:
		{
			UH_OFF;VH_OFF;WH_ON;//V- W+
			UL_OFF;VL_ON;WL_OFF;
			break;
		}
		case 3:
		{
			UH_OFF;VH_ON;WH_OFF;//U- V+
			UL_ON;VL_OFF;WL_OFF;
			break;
		}
		case 4:
		{
			UH_OFF;VH_ON;WH_OFF;//U- V+
			UL_ON;VL_OFF;WL_OFF;
			break;
		}
		case 5:
		{
			UH_OFF;VH_ON;WH_OFF;//V+ W-
			UL_OFF;VL_OFF;WL_ON;
			break;
		}
		case 6:
		{
			UH_ON;VH_OFF;WH_OFF;//U+ W-
			UL_OFF;VL_OFF;WL_ON;
			break;
		}
		default:
		{
			//1.关上管
			UH_OFF;VH_OFF;WH_OFF;
			//2.开下管
			UL_ON;VL_ON;WL_ON;
			break;
		}
	
	}
}


/************* 启动加速 ******************/
void Motor_Start(uint8_t direction)
{
	if(direction)
	{
		for(uint8_t i=100; i>0; i-=2)
		{
			for(uint8_t j=1; j<7; j++)
			{
				Six_step(j);
			}
			HAL_Delay(i+1);//最低1MS换相一次
		}
	}
}

/************* 电机匀速 ******************/
void Motor_Run(uint8_t direction)
{
	if(direction)
	{
			for(uint8_t j=1; j<7; j++)
			{
				Six_step(j);
				//HAL_Delay(1);
			}
	}
}

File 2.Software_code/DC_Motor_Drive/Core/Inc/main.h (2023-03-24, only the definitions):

#define KEY1_Pin GPIO_PIN_4
#define KEY1_GPIO_Port GPIOA
#define KEY2_Pin GPIO_PIN_5
#define KEY2_GPIO_Port GPIOA
#define UL_Pin GPIO_PIN_13
#define UL_GPIO_Port GPIOB
#define VL_Pin GPIO_PIN_14
#define VL_GPIO_Port GPIOB
#define WL_Pin GPIO_PIN_15
#define WL_GPIO_Port GPIOB
#define UH_Pin GPIO_PIN_8
#define UH_GPIO_Port GPIOA
#define VH_Pin GPIO_PIN_9
#define VH_GPIO_Port GPIOA
#define WH_Pin GPIO_PIN_10
#define WH_GPIO_Port GPIOA
#define IIC_SCL_Pin GPIO_PIN_15
#define IIC_SCL_GPIO_Port GPIOA
#define IIC_SDA_Pin GPIO_PIN_3
#define IIC_SDA_GPIO_Port GPIOB
#define LED0_Pin GPIO_PIN_4
#define LED0_GPIO_Port GPIOB
#define LED1_Pin GPIO_PIN_5
#define LED1_GPIO_Port GPIOB
#define BEEP1_Pin GPIO_PIN_6
#define BEEP1_GPIO_Port GPIOB

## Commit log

2023-02-21 A01.01:硬件原理图FOC部分移植
    [DC_Motor_Drive.PrjPcb, FOC_4.SchDoc, Main.SchDoc]
2023-02-23 C01.01:原理图完成MCU部分，确定硬件框架
    [DC_Motor_Drive.PrjPcb, Main.SchDoc]
2023-02-24 A01.02:完善原理图文档信息和README信息
    [FOC_4.SchDoc, Main.SchDoc]
2023-02-24 A01.03：整体原理图模块完成，网络标号待连接
    [Main.SchDoc]
2023-02-24 A01.04：除网络标号，原理图完成，请按要求添加封装
    [FOC_4.SchDoc, Main.SchDoc]
2023-02-24 原理图部分完成，网络标号已添加，请按要求添加封装
    [FOC_4.SchDoc, Main.SchDoc]
2023-02-24 更新README.md文件
2023-02-24 更新若干文件
    [DC_Motor_Drive.PrjPcb, FOC_4.SchDoc, Main.SchDoc]
2023-02-24 新建软件工程
2023-03-01 “修改管脚”
    [DC_Motor_Drive.PrjPcb, FOC_4.SchDoc, Main.SchDoc]
2023-03-01 “增加第三相电流反馈”
    [Main.SchDoc]
2023-03-01 “修改原理图，移除模块OLED，增加1.3‘OLED”
    [Main.SchDoc]
2023-03-02 A01.06:修改采集电压电阻值大小
    [DC_Motor_Drive.PrjPcb, FOC_4.SchDoc, Main.SchDoc]
2023-03-02 增加DCDC芯片文档
2023-03-02 输出原理图pdf
2023-03-02 增加参考文献
2023-03-07 修复原理图错误，增加封装
    [DC_Motor_Drive.PrjPcb, FOC_4.SchDoc, Main.SchDoc]
2023-03-07 PCB更新布局
    [DC_Motor_Drive.PrjPcb, FOC_4.SchDoc, Main.SchDoc]
2023-03-08 PCB布局基本完成，布线基本完成
    [Main.SchDoc]
2023-03-08 PCB完成，待添加丝印
2023-03-08 增加BOM表
    [07-BOM.xlsx]
2023-03-08 pcb外形修改
    [DC_Motor_Drive.PrjPcb]
2023-03-08 pcb完成，待评审
    [FOC_4.SchDoc]
2023-03-11 新增管脚对应表
    [08-管脚对应表.xlsx]
2023-03-11 新增代码初始化管脚
2023-03-11 A01.03:重写printf函数，修改至串口二
2023-03-11 A01.04:新增用户调度器(未验证)
2023-03-11 OLED移植成功(待验证)
2023-03-11 A01.06:采集四个通道的ADC数据(待验证)
2023-03-11 A01.07: 新增看门狗，溢出时间约6.5s(待验证)
2023-03-11 更新图片
2023-03-11 新增PCB的3D模型
2023-03-11 A01.07: 新增ADC校准，规范代码(待验证)
2023-03-13 增加蜂鸣器鸣响
2023-03-14 硬件文档命名
    [BLDC.SchDoc, DC_Motor_Drive.PrjPcb, FOC_4.SchDoc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]
2023-03-14 A01.09: 新增按键扫描函数(待验证)
2023-03-15 A01.0A: 调度器/OLED等外设测试通过
2023-03-15 A01.0B: 编码器功能初步测试通过
2023-03-20 update BLDC
    [BLDC.PrjPcb, Schlib1.SchLib, 原理图.SchDoc]
2023-03-21 update BLDC焊接文档
2023-03-22 Updata BLDC_Core
    [BLDC_Core.PrjPcb, 原理图.SchDoc]
2023-03-22 Updata KEY
    [KEY.PcbDoc, KEY.PrjPcb, KEY.SchDoc]
2023-03-24 A01.0C: 多级菜单功能完成
2023-03-25 更新BLDC_Core原理图
    [08-管脚对应表.xlsx, BLDC.PrjPcb, BLDC.SchDoc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]
2023-03-25 更新项目
    [STARTUP.OBJ, main.OBJ]
2023-03-25 A01.0D: 新增速度变量，实现编码器控制

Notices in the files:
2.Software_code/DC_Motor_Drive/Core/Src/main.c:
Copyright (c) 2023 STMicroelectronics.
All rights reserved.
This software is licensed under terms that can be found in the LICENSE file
